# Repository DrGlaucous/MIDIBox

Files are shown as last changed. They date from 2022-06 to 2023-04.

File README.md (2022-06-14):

### MIDI controllable music box
---

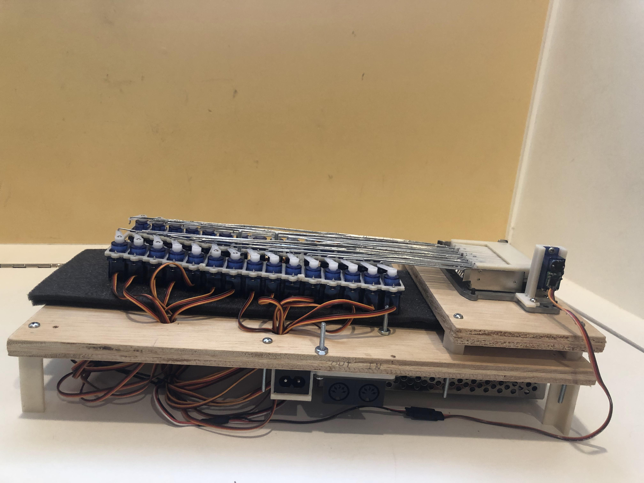
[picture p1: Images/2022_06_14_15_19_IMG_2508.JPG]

---
This repo contains all files that relate to the construction of my MIDI controlled music box. The design itself takes heavy inspiration from [mitxela's version](https://github.com/mitxela/musicbox), though everything seen here was made separately from scratch. 

I designed this with a goal to do absolutely no modification to the music box itself, aside from non-destructive disassembly. If desired, I could revert the music box back to its original, unmodified form even after the full MIDI conversion. 

Another notable difference between this design and the one by mitxela is the choice to use an external breakout board for MIDI interface rather than manually construct one with individual components. The interface I used was [this one by ubld.it](https://ubld.it/products/midi-breakout-board-mv-multi-voltage/). 

---
All relevant files can be found in the sub-folders in this repository.

For a demo, please see [this video](https://youtu.be/igBTrTq4vEI).

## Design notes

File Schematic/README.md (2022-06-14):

### Schematic
---
This is the wiring I used when soldering the control board for the music box. It doesn't have to be followed to the letter, as all pins are fully configurable in the firmware, but this is the simplest approach.

---

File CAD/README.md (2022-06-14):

### CAD
---
This folder contains the 3D models used to construct the actual music box machine. **Refer to pictures to see what needs to be constructed from this folder.**

The 2 main structure boards I used were simple rectangles of plywood cut to specs with the stencils in the `Vectors` folder.

For the 3D printed models, print the contents of the `STLs/FinalModels` folder.
With the pusher fingers, there are 2 models with 30 fingers each, both have intentionally different widths. It is best to print each of the varieties, and then mix and match them on the music box to get the proper spacing across the wafers. 

Source CAD files are in the `Source Models` folder. These are in .skp format, indented to be opened with sketchup 8 or newer. (In a pinch, you could even use the [sketchup webapp](https://app.sketchup.com/app) to open them.)

---

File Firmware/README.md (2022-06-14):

### Firmware
---
This folder contains the firmware that drives the MIDI controlled music box. It was originally designed around the ESP32 development board, but changed to work with the STM32 bluepill when I found that the ESP32 did not have the required amount of GPI/O pins for the project (31 + 2 for RX and TX, 33 total). Of course, you can use whatever board you wish, so long as it is compatible with the arduino `MIDI.h` library.

The STM32 only has 15 PWM pins, but needs to drive 31 servos, so the software is designed to do this with bit banging. To conserve CPU cycles and minimize servo chatter, servos are only attached when they are needed to push the note fingers.

With this project, I tried several different development platforms when programming the firmware. I started with the arduino IDE, then moved to visualMicro and eventually settled on PlatformIO to do the bulk of my programming.

If, for some reason, you *really* don't want to use PlatformIO to upload the firmware *(though I highly suggest you do, it is much better than the stock IDE)*, you should be able to use the standard arduino IDE and open the main.cpp file in the source directory. You will need to find and remove any `#ifdef STM32` preprocessor statements or you will run into compile errors. This is only defined in the platformIO config file.

---
The final firmware is in the "PlatformIO" folder, and the old stuff is in the "Deprecated" folder.

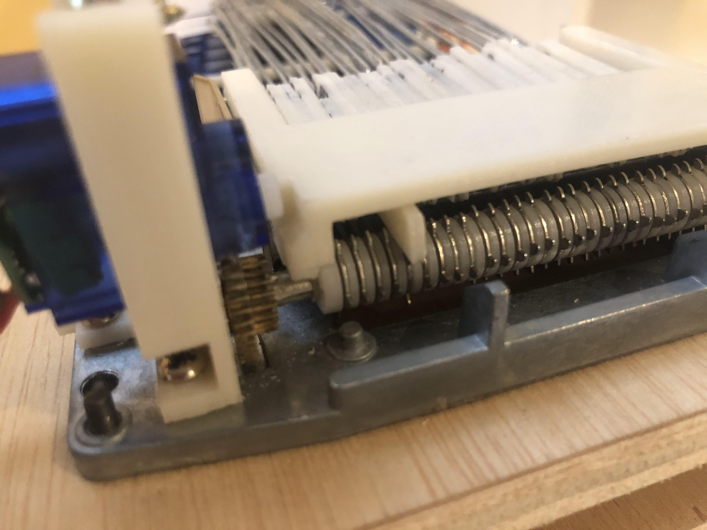
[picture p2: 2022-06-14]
Images/2022_06_14_15_21_IMG_2514.JPG

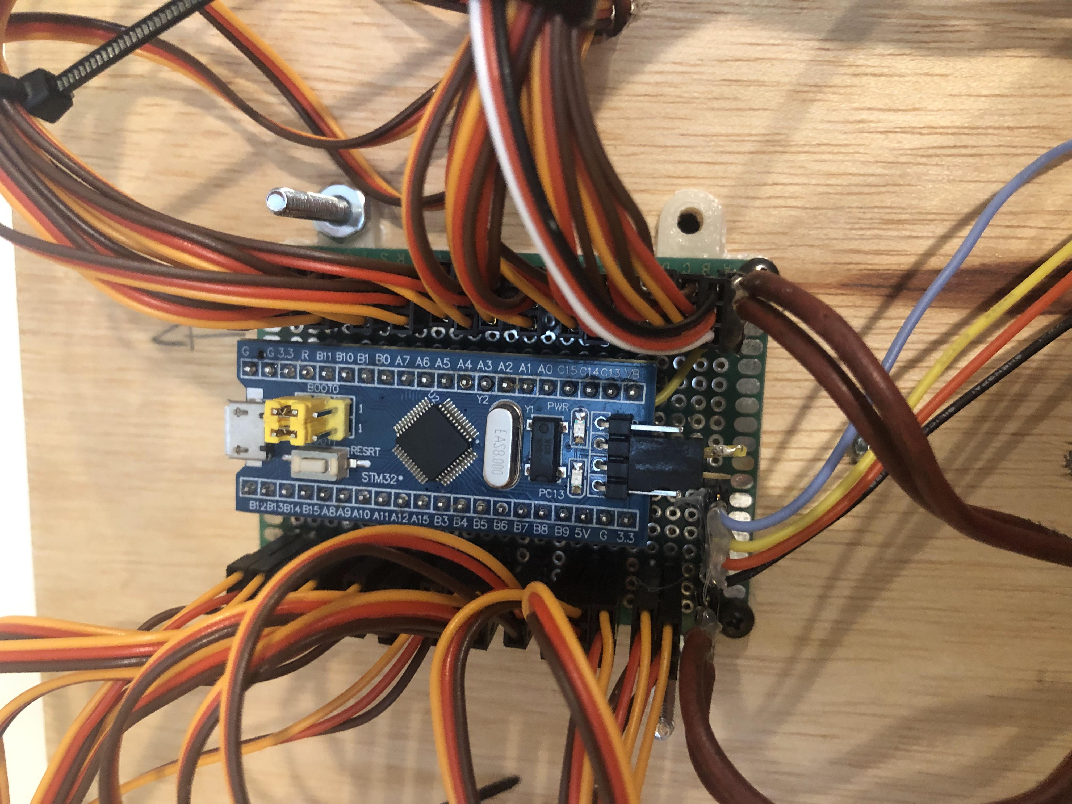
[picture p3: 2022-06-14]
Images/2022_06_14_15_22_IMG_2516.JPG

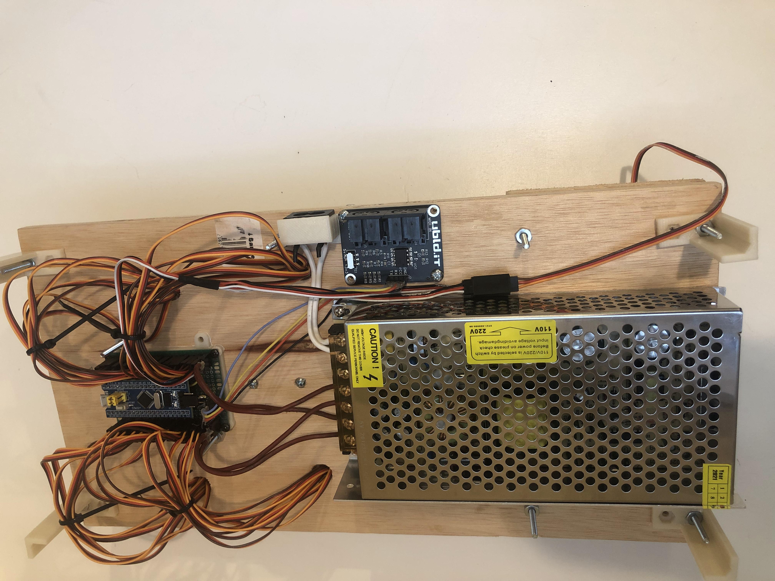
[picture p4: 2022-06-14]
Images/2022_06_14_15_22_IMG_2515.JPG

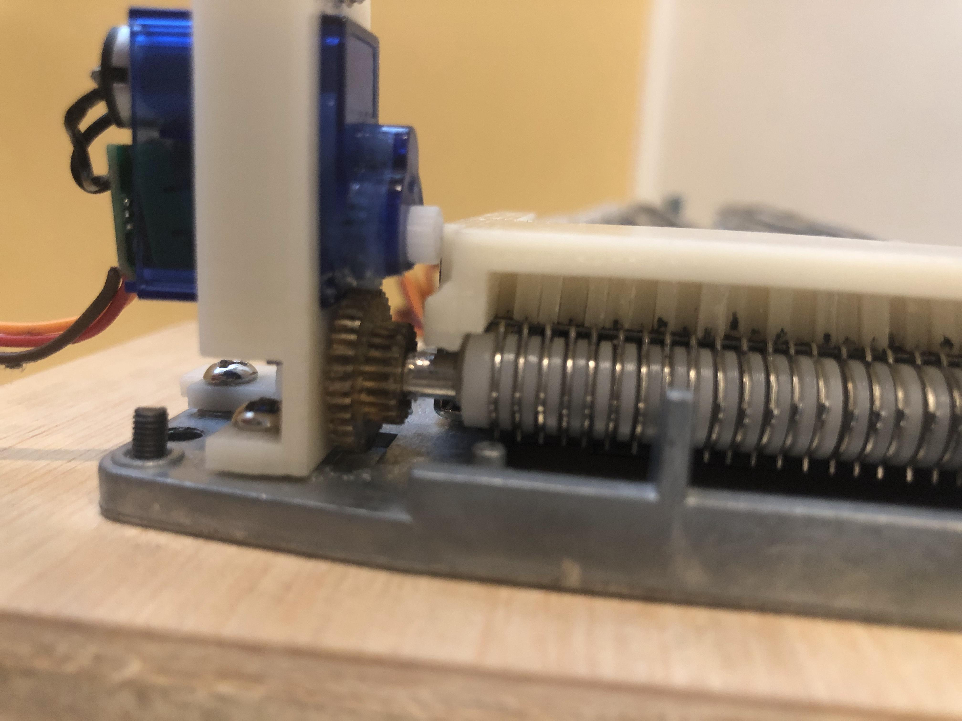
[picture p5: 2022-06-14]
Images/2022_06_14_15_20_IMG_2511.JPG

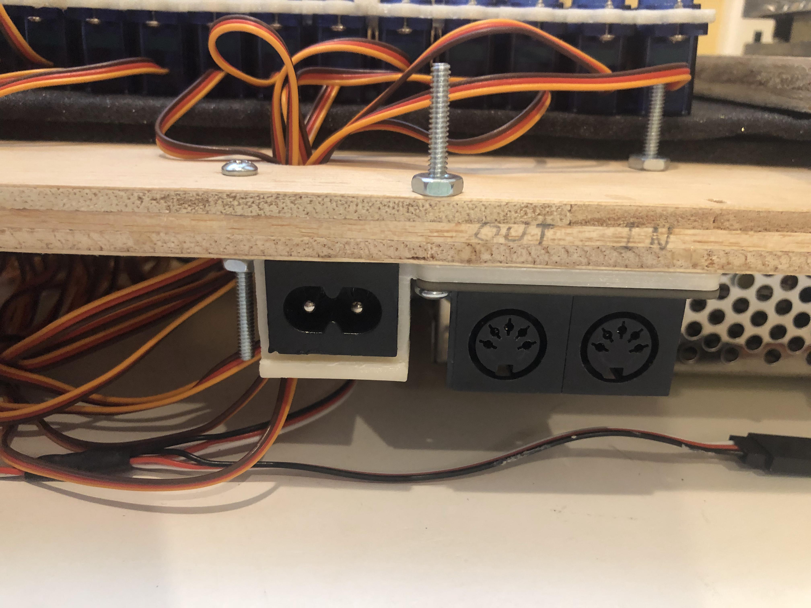
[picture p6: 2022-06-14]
Images/2022_06_14_15_20_IMG_2510.JPG

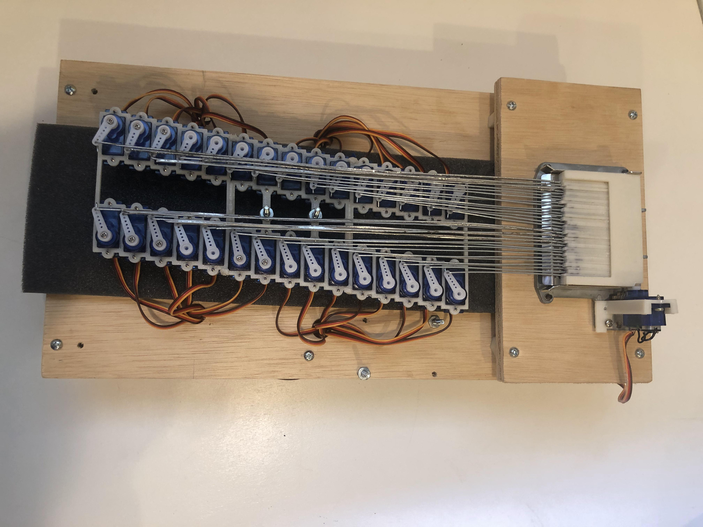
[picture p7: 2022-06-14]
Images/2022_06_14_15_20_IMG_2509.JPG

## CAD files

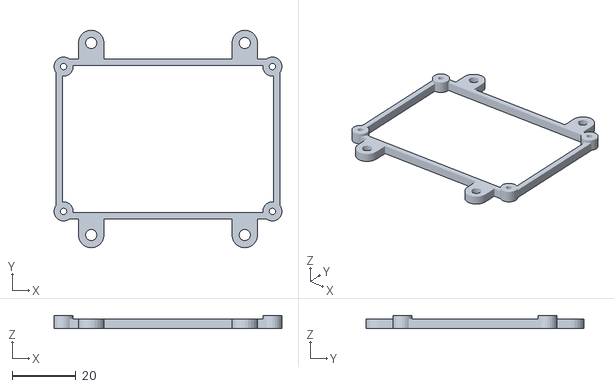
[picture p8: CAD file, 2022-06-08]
CAD/STLs/FinalModels/MainboardBracket.stl
71.2 x 68.0 x 4.00

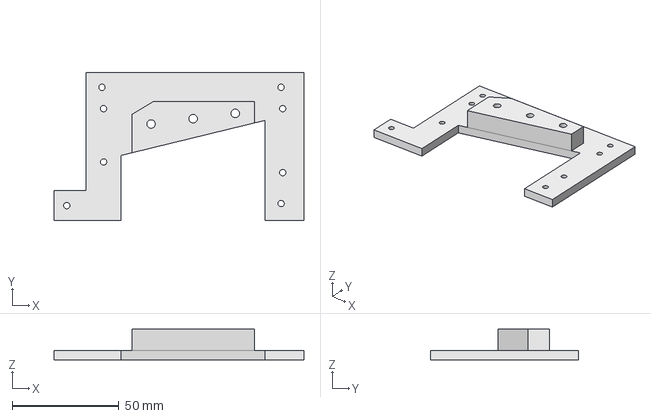
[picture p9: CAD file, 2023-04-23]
CAD/Source Models/Harp.step
117.2 x 69.5 x 14.5 mm

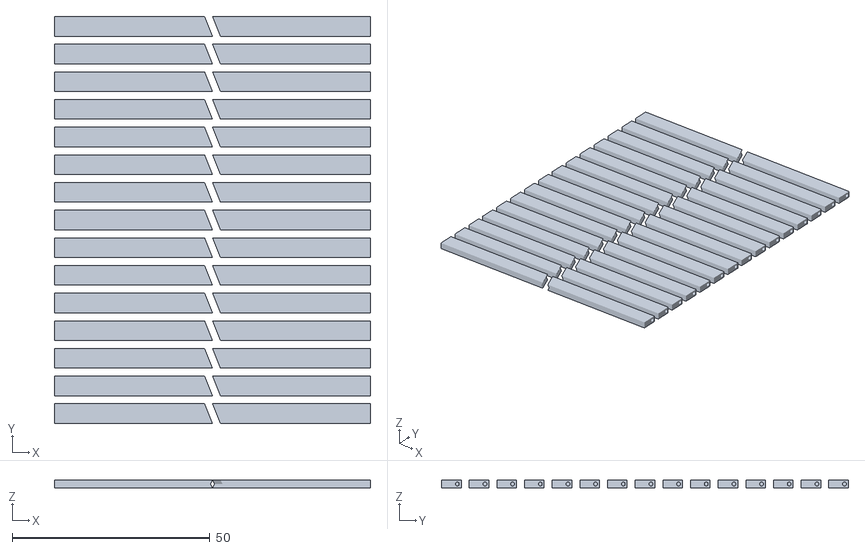
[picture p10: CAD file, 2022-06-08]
CAD/STLs/FinalModels/Finger2x5mm X30.stl
80.0 x 103.0 x 2.00

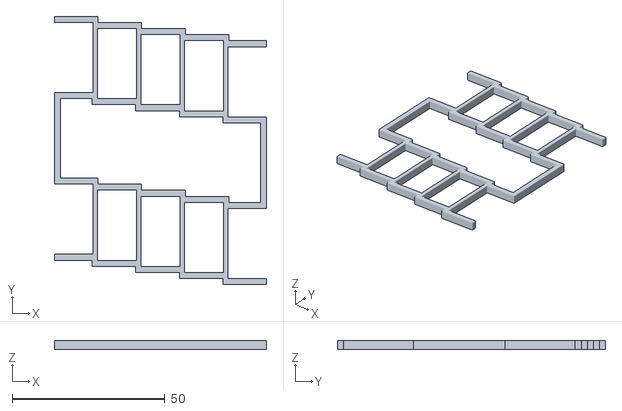
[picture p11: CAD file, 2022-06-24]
CAD/STLs/ServoNoteRackBottomMiddle.stl
69.5 x 88.0 x 3.00

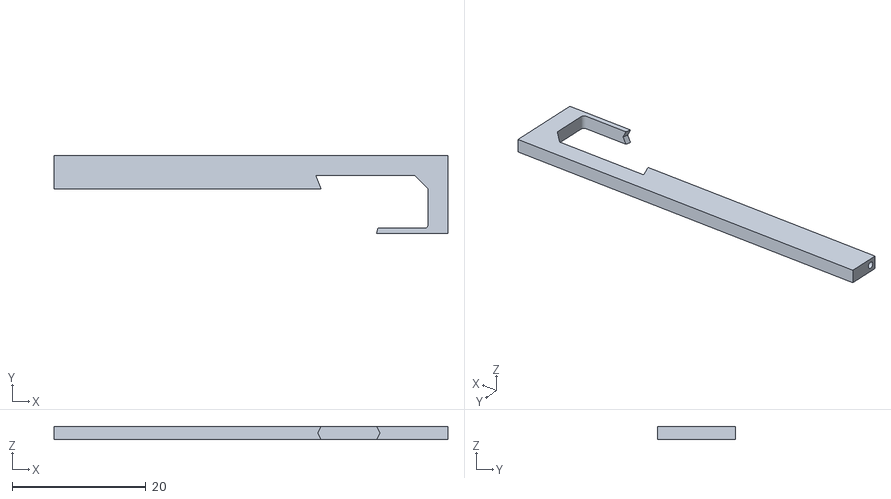
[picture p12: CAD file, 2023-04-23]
CAD/STLs/TestModels/SelfReturningFinger.stl
59.0 x 11.7 x 2.00

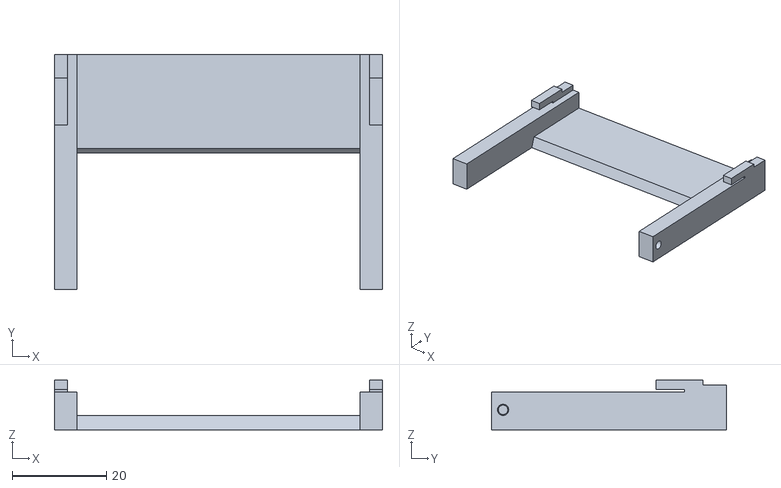
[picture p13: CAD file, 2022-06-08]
CAD/STLs/FinalModels/FingerGuideV2_5mm.stl
69.7 x 50.0 x 10.6

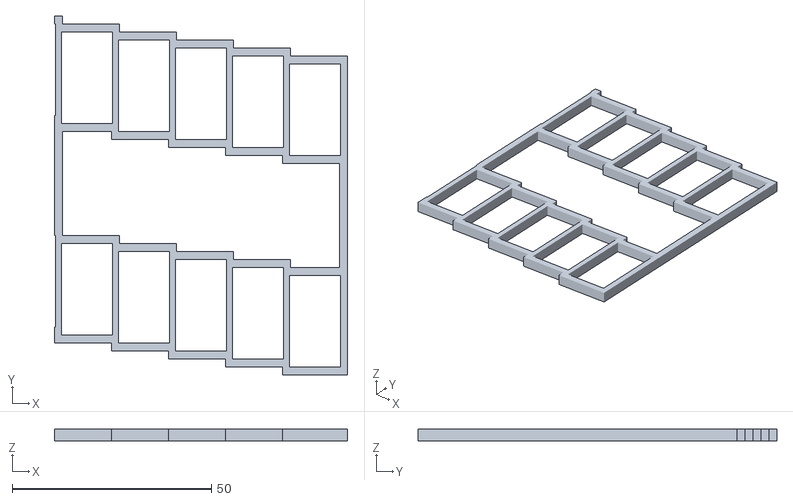
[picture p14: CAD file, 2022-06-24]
CAD/STLs/ServoNoteRackBottomSides.stl
73.5 x 90.0 x 3.00

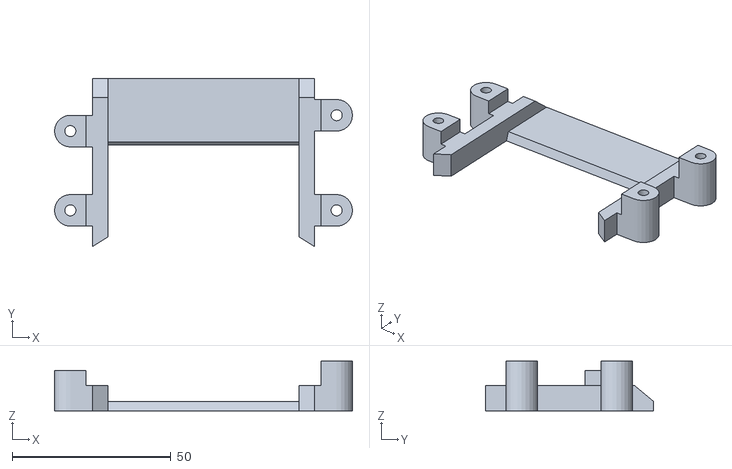
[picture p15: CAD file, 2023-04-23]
CAD/STLs/TestModels/Roof.stl
94.0 x 53.0 x 15.7

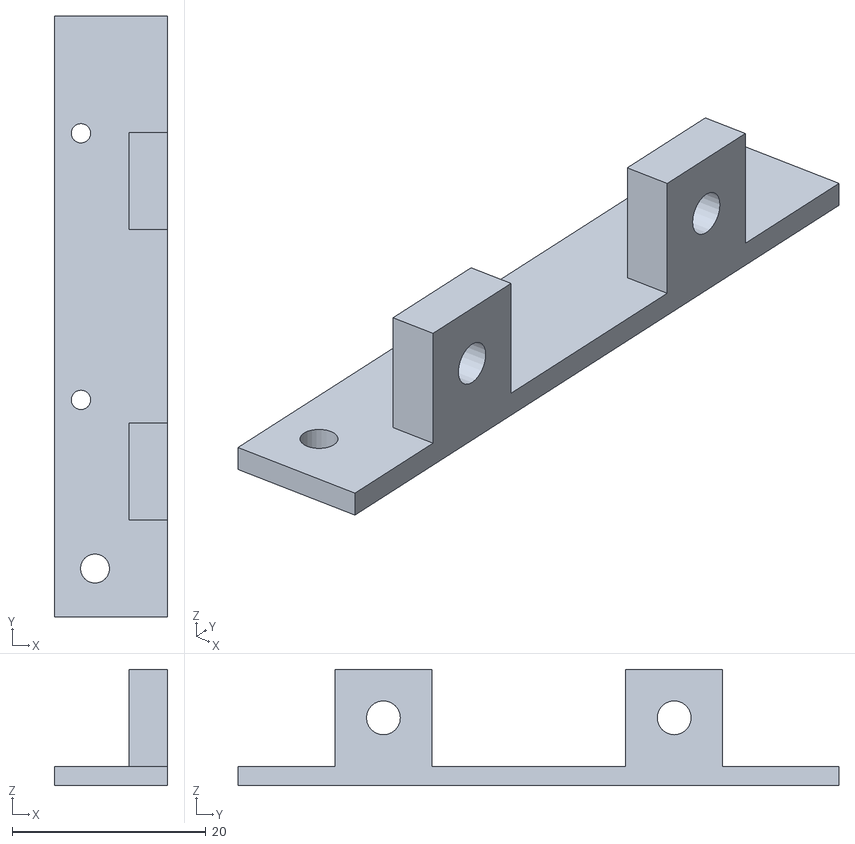
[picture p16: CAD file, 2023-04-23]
CAD/STLs/TestModels/WallLeft.stl
11.7 x 62.0 x 12.0

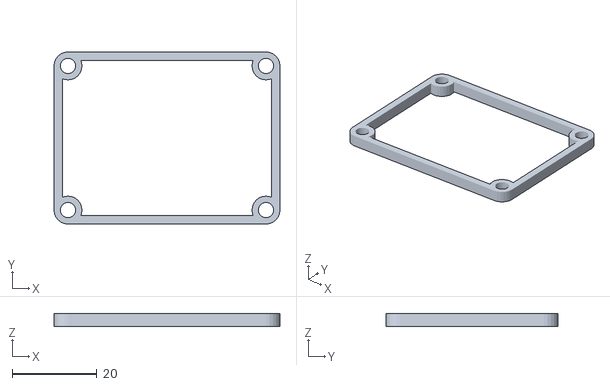
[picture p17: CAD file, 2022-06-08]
CAD/STLs/FinalModels/MIDIBreakoutBracket.stl
53.3 x 40.6 x 3.00

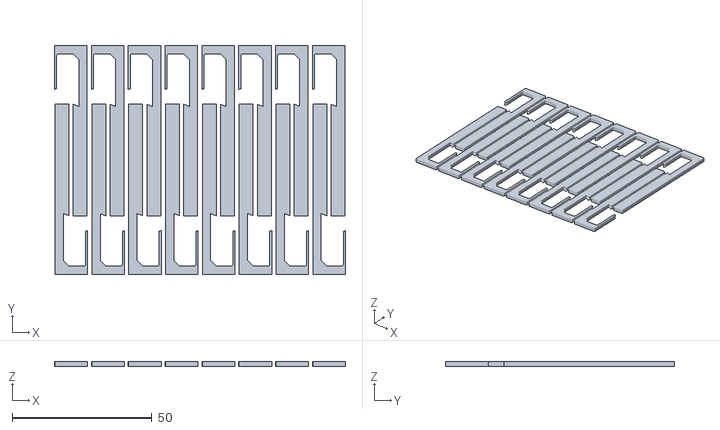
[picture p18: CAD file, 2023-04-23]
CAD/STLs/TestModels/1.8mFingerPlate.stl
104.3 x 82.0 x 1.80

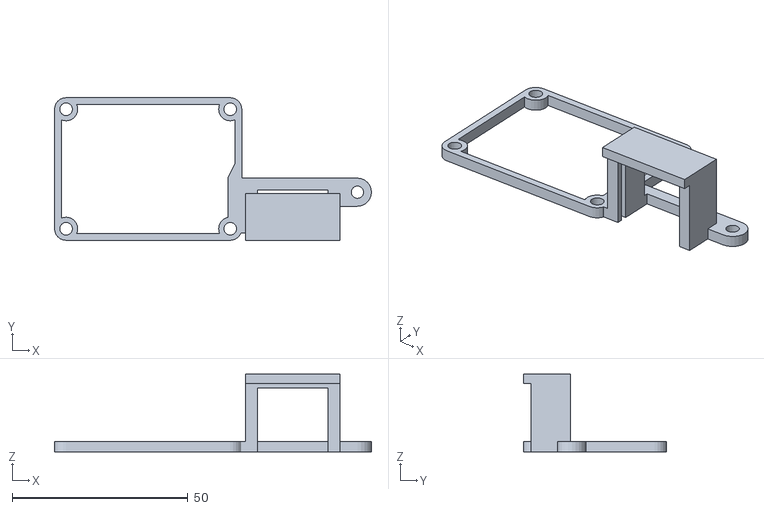
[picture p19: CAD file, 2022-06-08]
CAD/STLs/FinalModels/MIDIBreakout and Power Bracket.stl
90.2 x 40.6 x 22.1

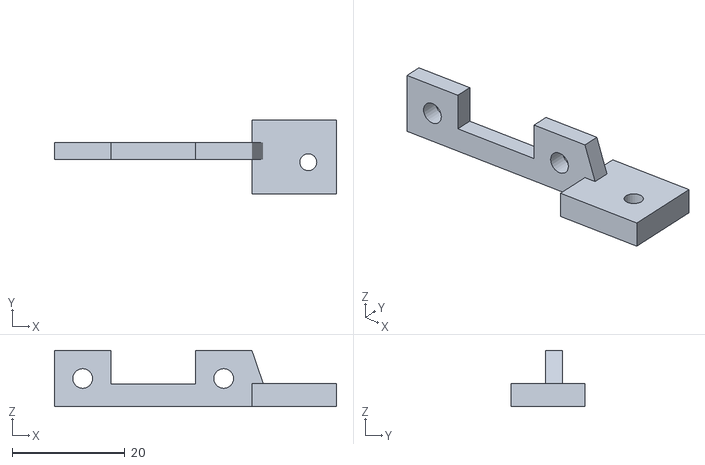
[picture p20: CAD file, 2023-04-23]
CAD/STLs/TestModels/DrumMount.stl
50.0 x 13.1 x 10.0

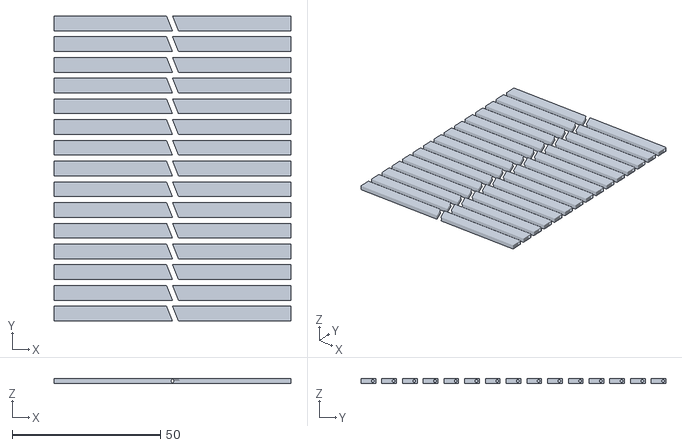
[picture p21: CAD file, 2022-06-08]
CAD/STLs/FinalModels/Finger1.8x5mm X30.stl
80.0 x 103.0 x 1.80

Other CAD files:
CAD/STLs/TestModels/SelfReturningFingerV2.stl
CAD/STLs/FinalModels/SupportLeg.stl
CAD/STLs/TestModels/SelfReturningFingerX4.stl
CAD/STLs/FinalModels/MovementStand.stl
CAD/STLs/FinalModels/ServoNoteRack.stl
CAD/STLs/FinalModels/ServoNoteRackMiddle.stl
CAD/STLs/FinalModels/ServoNoteRackSides.stl
CAD/STLs/TestModels/2mFingerPlate.stl
CAD/STLs/TestModels/Finger.stl
CAD/STLs/TestModels/Finger1.8x5mm.stl
CAD/STLs/TestModels/FingerGuide.stl
CAD/STLs/TestModels/FingerShimVariety.stl
CAD/STLs/TestModels/Finger_x30.stl
CAD/STLs/TestModels/HarpFrame.stl
CAD/STLs/TestModels/SelfReturningFingerV2_X4.stl
CAD/STLs/TestModels/ServoMountInsulatedPart1.stl
CAD/STLs/TestModels/ServoMountInsulatedPart2.stl
CAD/STLs/TestModels/ServoMountTest.stl
CAD/STLs/TestModels/WallKit.stl
CAD/STLs/TestModels/WallRight.stl
CAD/Source Models/Harp.FCStd
CAD/Source Models/Harp.SLDASM
CAD/Source Models/vectorExport.skp

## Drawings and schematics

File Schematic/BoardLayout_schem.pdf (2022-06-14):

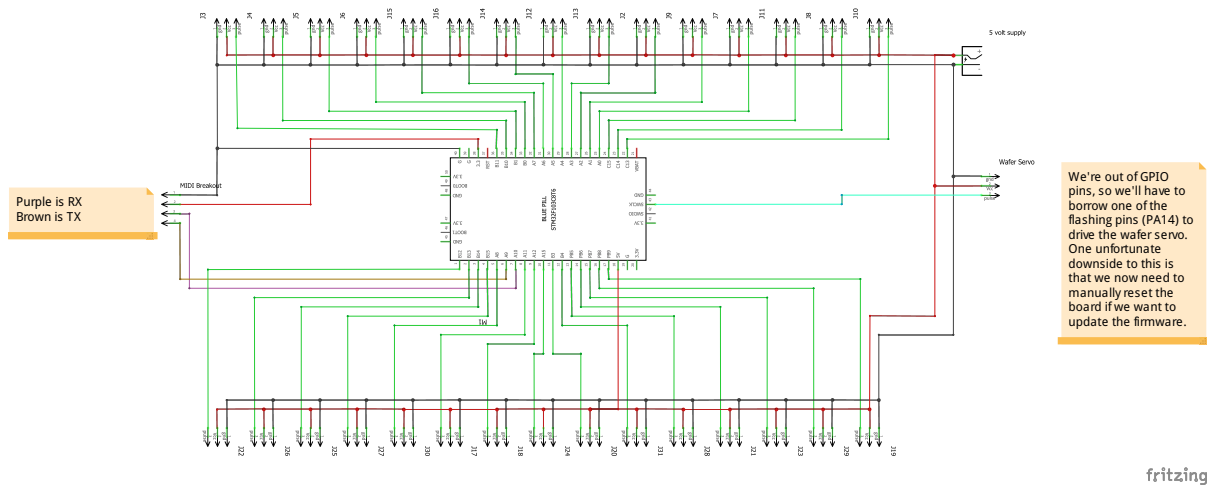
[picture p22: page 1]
ple is; fla; hin g; pin s; rive

pin
rvo. One unfortunate downside to this is that we now need to manually reset the board if we want to update the firmware.

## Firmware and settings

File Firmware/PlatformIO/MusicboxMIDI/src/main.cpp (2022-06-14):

/*
 Name:		ESP32MIDI.ino
 Created:	5/6/2022 6:17:48 PM
 Author:	Dr. G
*/

#include <MIDI.h>
#include <Arduino.h>
//#include <Control_Surface.h>//an alternate MIDI library, but is not compatible with the STM32 (I originally inteded to use an ESP32)
#include "configuration.h"
#include "ServoHandler.h"

//for STM32 boards, Serial is Serial1
#ifdef USING_STM32
MIDI_CREATE_INSTANCE(HardwareSerial, Serial1, MIDI);
#else
MIDI_CREATE_INSTANCE(HardwareSerial, Serial, MIDI);
#endif

//some more control surface-alternative stuff
/*
HardwareSerialMIDI_Interface MIDI_SERIAL = Serial;
BluetoothMIDI_Interface MIDI_BLE;

// Custom MIDI callback that prints incoming messages.
struct MyMIDI_Callbacks : FineGrainedMIDI_Callbacks<MyMIDI_Callbacks> {
    // Note how this ^ name is identical to the argument used here ^

    // Function that is called whenever a MIDI Note Off message is received. (This is not important when playing notes of a fixed length (I.E a music box))
    //void onNoteOff(Channel channel, uint8_t note, uint8_t velocity, Cable cable) {
    //    digitalWrite(5, 0);
    //}

    // Function that is called whenever a MIDI Note On message is received.
    void onNoteOn(Channel channel, uint8_t note, uint8_t velocity, Cable cable) {
        
        for (int i = 0; i < SERVO_COUNT; ++i)
        {
            if (SMT[i].noteNo == note)
            {
                SMT[i].requestNote = true;
            }
        }

    }

} callback;
*/

//System clock
void GetTicks(void)
{
	LastMillisecondTicks = MillisecondTicks;
	LastMicrosecondTicks = MicrosecondTicks;

	MillisecondTicks = millis();
	MicrosecondTicks = micros();
}


// Function that is called whenever a MIDI Note On message is received.
void onNoteOn(uint8_t channel, uint8_t pitch, uint8_t velocity) {

    //digitalWrite(PC13, false);//this LED is inverted: "false" is actually "on"

    for (int i = 0; i < SERVO_COUNT; ++i)
    {
        if (SMT[i].noteNo == pitch)
        {
            SMT[i].requestNote = true;
        }
    }

}
//this was needed for debugging, but not for the final firmware
/*void onNoteOff(uint8_t channel, uint8_t pitch, uint8_t velocity)
{
    //digitalWrite(PC13, true);

}*/


void setup() {


    //old control surface stuff
    //MIDI_SERIAL.begin(); // Initialize midi interface
    //MIDI_SERIAL.setCallbacks(callback);
    //MIDI_BLE.begin(); // Initialize midi interface
    //MIDI_BLE.setCallbacks(callback);


    //tie callbacks to midi events
    MIDI.setHandleNoteOn(onNoteOn);
    //MIDI.setHandleNoteOff(onNoteOff);//this was needed for debugging, but not for the final firmware
    MIDI.begin();


    SetupServo();

}


void loop() {

    GetTicks();


    //an effort to conserve cycles by only calling this once per millisecond
    if( MillisecondTicks != LastMillisecondTicks)//% 1000 == 0)
    {
        MIDI.read();
    }


    //old control surface stuff
    //MIDI_SERIAL.update(); // Update the Control Surface
    //MIDI_BLE.update();
    


    //perform servo actions
    AllServoSweep();
    AllServoDrive();
    WaferServoDrive();




}

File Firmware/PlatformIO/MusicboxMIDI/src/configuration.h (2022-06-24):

//Configuration
//this program was built using PlatformIO.
//with some tweaks, it COULD be built using the arduino IDE enviroment. All libraries used in this project are arduino


//this is not really needed, but I have it here for my personal reference. the arduino IDE doesn't like it here, but platformIO doesn't mind
#ifndef USING_STM32
// Note: this needs to match with the PIN_MAP array in board.cpp
//STM32 pin mapping
enum {
    PA0, PA1, PA2, PA3, PA4, PA5, PA6, PA7, PA8, PA9, PA10, PA11, PA12, PA13,PA14,PA15,
	PB0, PB1, PB2, PB3, PB4, PB5, PB6, PB7, PB8, PB9, PB10, PB11, PB12, PB13,PB14,PB15,
	PC13, PC14,PC15
};
#endif



//the state of a pin when it is "high" or "clicked" (nothing actually uses this in the code, but its useful for debugging)
#define ON_STATE 0

//number of notes on the music box
#define SERVO_COUNT 30
#define SERVO_PUSH_TIME 360//in Milliseconds (1K == 1 second)


#define CONTINUOUS_REST_ANGLE 1500//the angle the continuous rotation servo will be set to "at rest"
#define CONTINUOUS_ACTIVE_ANGLE 700//the angle it uses when rotating (i believe the more different it is from the rest angle, the faster the servo will go)
#define CONTINUOUS_SERVO_PIN PA14//PA14//pin for this servo (I use PC13 for debugging)
#define CONTINUOUS_RUN_TIME 500//time in milliseconds the servo will spin





#define SMOOTH_SWEEP//sweeps the servo at a controlled rate, giving steps of angles. if not defined, servos will sweep with only the min and max angles (this is faster, but less well-timed)

//#define WAIT_UNTIL_DONE//will not try to play another note on the servo until it has retracted fully

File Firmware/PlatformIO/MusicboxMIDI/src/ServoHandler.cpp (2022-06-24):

#include <Arduino.h>
#include "configuration.h"
#include "ServoHandler.h"
//#include <Control_Surface.h>


//Servo Map Table
SERVO_ID SMT[] =
{
	//pin, note, minRange, maxRange, currentPPM, requestNote, goForward, dwellTime, 
	//main side (forwards)
	{PB12, 53, 900, 1500, 900, false, false, 0},//0**lowest note, going up
	{PB13, 55, 950, 1500, 950, false, false, 0},//1**
	{PB14, 60, 1040, 1700, 1040, false, false, 20},//2**
	{PB15, 62, 950, 1650, 950, false, false, 0},//3
	{PA8, 64, 1000, 1530, 1000, false, false, 30},//4**
	{PA11, 65, 1000, 1550, 1000, false, false, 0},//5USB- (unplug these two for USB serial)
	{PA12, 67, 970, 1600, 970, false, false, 0},//6USB+
	{PA15, 69, 950, 1600, 950, false, false, 0},//7
	{PB3, 70, 1050, 1600, 1050, false, false, 0},//8
	{PB4, 71, 950, 1550, 950, false, false, 0},//9
	{PB5, 72, 1000, 1600, 1000, false, false, 0},//10**C
	{PB6, 73, 950, 1500, 950, false, false, 0},//11**C#
	{PB7, 74, 950, 1550, 950, false, false, 0},//12**D
	{PB8, 75, 1000, 1600, 1000, false, false, 0},//13**
	{PB9, 76, 1000, 1600, 1000, false, false, 0},//14**
	//port side (backwards)
	{PB11, 77, 1500, 900, 1500, false, false, 0},//15**F mid-note, going up
	{PB10, 78, 1600, 970, 1600, false, false, 0},//16**
	{PB1, 79, 1470, 900, 1470, false, false, 40},//17**G
	{PB0, 80, 1600, 1000, 1600, false, false, 0},//18**
	{PA7, 81, 1530, 1000, 1530, false, false, 30},//19**A
	{PA6, 82, 1600, 1000, 1600, false, false, 0},//20**
	{PA5, 83, 1500, 950, 1500, false, false, 0},//21**B
	{PA4, 84, 1420, 900, 1420, false, false, 40},//22**C
	{PA3, 85, 1600, 1000, 1600, false, false, 0},//23**
	{PA2, 86, 1500, 900, 1500, false, false, 0},//24**D
	{PA1, 87, 1420, 900, 1420, false, false, 50},//25**
	{PA0, 88, 1530, 970, 1530, false, false, 20},//26**E borrowed
	{PC15, 89, 1600, 1050, 1600, false, false, 0},//27**ditto
	{PC14, 91, 1580, 980, 1580, false, false, 0},//28**
	{PC13, 93, 1500, 950, 1500, false, false, 0},//29**highest note//PC13 (when debugging, I use placeholder PB2 so I can connect the stlink (the wafer servo uses this pin))
};



SERVO_ID CONTINUOUS_SERVO =
	//pin, note, minRange, maxRange, currentPPM, requestNote, goForward
	{CONTINUOUS_SERVO_PIN, 0, CONTINUOUS_REST_ANGLE, CONTINUOUS_ACTIVE_ANGLE, CONTINUOUS_REST_ANGLE, false, false};


//these should be with the GetTicks() function, but in order to use them in other pages, I would need to make another header file, and I'm lazy
unsigned long MillisecondTicks{};
unsigned long MicrosecondTicks{};
unsigned long LastMillisecondTicks{};//previous values
unsigned long LastMicrosecondTicks{};

//unsigned char isFinished{};//use the char to store several booleans


//pinMode all the output pins
void SetupServo(void)
{
	//note servos
	for (int i = 0; i < SERVO_COUNT; ++i)
	{
		SMT[i].activeTime = 0;//initialize this variable
		pinMode(SMT[i].pinNo, OUTPUT);

	}

	//wafer servo
	pinMode(CONTINUOUS_SERVO.pinNo, OUTPUT);

}

//send the correct pulses to the servo
void ServoBackend(SERVO_ID *tower)
{
	//global servo clock
	//every 20 Milliseconds, we will set all servo pins to HIGH
	//and then turn them off if the microsecond count is >= to the value prescribed

	//used to get the change in microseconds every 20 Milliseconds
	static unsigned long divyMicroseconds{};
	static unsigned long previousMicrosecondTick{};

	//static bool MillisecondTickHasReset{};//to save on math and only calulate this one time per cycle


	if (MillisecondTicks != LastMillisecondTicks && MillisecondTicks % 20 == 0)// !(isFinished & SERVO_HIT_REFRESH))
	{
		//handy note: '|=' adds a binary flag, '&= ~' removes it

		//moved the for() loops outside this function

		previousMicrosecondTick = MicrosecondTicks;


		//set servo pin to HIGH every 20 milliseconds
		digitalWrite(tower->pinNo, true);
		
	}
	else
	{

		//get the passage of microseconds
		divyMicroseconds = MicrosecondTicks - previousMicrosecondTick;

		
		if (tower->currentPPM < divyMicroseconds)
		{
			digitalWrite(tower->pinNo, false);
		}
		

	}



}

//drives the note servos
void AllServoDrive(void)
{
	for(int i = 0; i < SERVO_COUNT; ++i)
	{
		//will not run the servo if it is not being used
		if(SMT[i].activeTime < SERVO_PUSH_TIME + (SERVO_PUSH_TIME / 2))//I've added a little extra time for the servo to make it back
			ServoBackend(&SMT[i]);
		//else if(SMT[i].pinNo == PA7)//for debugging
		//	ServoBackend(&SMT[i]);

	}

}



//drives the wafer spinner servo
void WaferServoDrive(void)
{

	static unsigned int waferTimeout{1000};
	//static bool waferSpeedSet{};

	for(int i = 0; i < SERVO_COUNT; ++i)
	{
		//if any servo is currently playing a note
		if(SMT[i].goForward == true)
		{
			waferTimeout = 0;	
		}	
	}

	//once every millisecond
	if (MillisecondTicks != LastMillisecondTicks)
	{
		++waferTimeout;
	}

	//this will only attach the servo if it needs to be run, which will save CPU cycles
	if(waferTimeout < CONTINUOUS_RUN_TIME)
	{
		//digitalWrite(PC13, false);

		CONTINUOUS_SERVO.currentPPM = CONTINUOUS_SERVO.maxRange;
		ServoBackend(&CONTINUOUS_SERVO);
	}
	//this conditional was only needed for debugging
	/*else
	{
		//digitalWrite(PC13, true);
		CONTINUOUS_SERVO.currentPPM = CONTINUOUS_SERVO.minRange;
		ServoBackend(&CONTINUOUS_SERVO);
	}*/


}

//sweep each servo when a trigger variable is called
void SingleServoSweep(SERVO_ID *tower)
{


	if (tower->requestNote == true)
	{
		tower->requestNote = false;
#ifdef WAIT_UNTIL_DONE
		if(tower->activeTime >= SERVO_PUSH_TIME)//will only push again if the tower has been active for at least the required ammount
		{
			tower->goForward = true;
			tower->activeTime = 0;
		}
#else
		tower->goForward = true;
		tower->activeTime = 0;
#endif

	}
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

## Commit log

2022-05-15 Added CAD files
    Condensed CAD and firmware into one location (this repository)
    [Finger.stl, FingerGuide.stl, Finger_x30.stl]
2022-05-20 big updates
    trying out PlatformIO as the development environment and merging CAD files into the local repository for easy updating
2022-05-23 Updated PlatformIO firmware
    Made the program compatible with the STM32 BluePill because it has the needed GPIO ports for the project
    [configuration.h]
2022-05-24 some little code cleanup
    that's all
    [configuration.h]
2022-05-26 CAD work
    I sure hope it does
    [ServoMountTest.stl, ServoNoteRack.stl, ServoNoteRackMiddle.stl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]
2022-05-28 More CAD work
    [MovementStand.stl, SupportLeg.stl, vectorExport.skp]
2022-06-08 updated everything
    better CAD, better CODE, more physical progress
    [BoardLayout.fzz, Finger1.8x5mm X30.stl, Finger1.8x5mm.stl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]
2022-06-14 Finished first iteration
    The music box works, so I've organized the repo and added documentation.
    [Finger.stl, Finger1.8x5mm X30.stl, Finger1.8x5mm.stl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]
2022-06-24 Parts and firmware update
    created a bracket to take the flex out of the servo rack and gave the firmware more features
    [ServoMountInsulatedPart1.stl, ServoMountInsulatedPart2.stl, ServoNoteRackBottomMiddle.stl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]
2023-04-23 Updating fingers to remove need for spinner motor
    Also making new harp base
    [1.8mFingerPlate.stl, 2mFingerPlate.stl, DrumMount.stl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]
